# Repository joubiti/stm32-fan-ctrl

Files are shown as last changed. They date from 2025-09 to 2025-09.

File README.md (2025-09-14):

# 12V Fan Controller with STM32 and PID control
## Overview

This project implements a closed-loop fan controller on a custom 4-layer PCB (manufactured at JLCPCB) with an STM32G0 micrcontroller.
The fan speed is controlled using a PWM signal and regulated to a target RPM using a PID controller.
The tachometer output of the fan is measured with a timer input capture unit, filtered, and fed into the control loop.
Fairly satisfactory control performances have been achieved with Kp=0.01, Ki=0.015, and Kd = 0.001 at 10Hz.



## Hardware features

4 layer board designed with KiCAD, and manufactured at JLCPCB for roughly 100 euros total (including shipping) for 2PCBA and 3PCBs, very minimal and cheap BOM. Production files are in Hardware/Production.

* **Buck Converter** takes 12V input from DC input jack and generates 5V rail (for PWM)
* **Linear Regulator** generates 3.3V rail from 5V (for MCU signals)
* **N-channel MOSFET** for low-side switching to generate appropriate PWM signals for 4-wire fan, inverting logic in firmware
* **Tachometer** open collector input for fan RPM measurement (hardware timer)

Schematics are given below:



PCB layout:



3D view:



Manufactured & assembled boards:





## System Architecture

* **Tachometer**: Measures period between tach pulses, converts to RPM (tachometer.h, tachometer.c)
* **First order IIR low pass filter**: Smooths RPM measurement (low_pass_filter.h, low_pass_filter.c)
* **PID controller**: Computes duty cycle command from target vs. measured RPM (pid_controller.h, pid_controller.c)
* **Fan speed controller**: Applies PWM duty cycle to MOSFET (fan_speed_controller.h, fan_speed_controller.c)
* **Application loop**: Handles control functions at 10 Hz, heartbeat at 1Hz, logging at 0.5Hz

```
  while (1)
  {
    /**************************** CONTROL LOOP (10 Hz) ****************** */
    tachometer_update_rpm(&fan_tachometer, HAL_GetTick());
    low_pass_filter_update(&rpm_filter, fan_tachometer.current_rpm, HAL_GetTick());
    uint8_t command = pid_controller_step(&pid, (uint32_t)rpm_filter.last_sample, RPM_SETPOINT, HAL_GetTick());
    if(command != PID_NO_UPDATE)
    {
      fan_set_rpm_percent(&fan_controller, command);
    }
    /******************************************************************** */

    /************************** HEARTBEAT LED & PERIODIC UART MESSAGES ****** */
    heartbeat_toggle(&heartbeat_led, HAL_GetTick());
    logging_send_periodic_msg(HAL_GetTick(), "Fan RPM: %d \n", fan_tachometer.current_rpm);
    /************************************************************************ */
  }
```

## System performances

After tuning PID controller and testing various setpoints, we have reached the following system response.

For 5000 RPM:

For 8000 RPM:

It's possible to achieve better performances, but for the sake of this project and for my use-case, this is satisfying enough.
The plots were generated with MCUViewer, which enables live capture of global variables with static addresses through SWD/JTAG.



## Building

To build the code, it is enough to run "make" in the "Software" directory. Assuming arm-none-eabi-gcc is correctly installed and configured for $PATH.
KiCAD Files are provided in Hardware/, and JLCPCB production files in Hardware/Production.

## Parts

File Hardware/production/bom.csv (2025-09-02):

Designator | Footprint | Quantity | Value | LCSC Part #
C1, C2, C3, C7 | 0402 | 4 | 100n
C10, C11, C12, C13, C8 | 1206 | 5 | 10u
C4 | 0402 | 1 | 4.7u
C5, C6 | 0402 | 2 | 10p
C9 | 1206 | 1 | 10n
CN1 | CONN-TH_4P-P3.50_DIBO_DB127S-3.5-4P-GN | 1 | DB127S-3.5-4P-GN | C2997511
D1 | 0805 | 1 | LED
D2 | 0402 | 1 | LED
D3 | SOD-123_L2.7-W1.6-LS3.7-RD-1 | 1 | B5819W_C8598 | C8598
F1 | 1206 | 1 | 500mA
FB1 | 1206 | 1 | 600 @ 600 MHz
L1 | 1206 | 1 | 4.7u
Q1 | SOT-23_L2.9-W1.3-P1.90-LS2.4-BR | 1 | AO3401A | C15127
Q2 | Q_SOT-23 | 1 | AO3400A | C20917
R1 | R_0603 | 1 | 49k9
R10, R13, R9 | R_0603 | 3 | 10k
R11, R3 | R_0402 | 2 | 10k
R12 | R_0402 | 1 | 100
R2, R8 | R_0402 | 2 | 1k
R4 | R_0603 | 1 | 100k
R7 | R_0603 | 1 | 9k1
TP1, TP2, TP3, TP5, TP6 | TestPoint_Pad_D3.0mm | 5 | TestPoint
TP10, TP11, TP9 | TestPoint_THTPad_D1.0mm_Drill0.5mm | 3 | TestPoint
TP4, TP7, TP8 | TestPoint_Pad_D2.0mm | 3 | TestPoint
U1 | LQFP-64_L10.0-W10.0-P0.50-LS12.0-BL | 1 | STM32G070RBT6 | C529340
U2, U3 | HDR-TH_3P-P2.54-V-M-1 | 2 | 826629-3 | C306127
U4 | SOT-23-6_L2.9-W1.6-P0.95-LS2.8-BR | 1 | MP2359DT-LF-Z | C6595509
U5 | DC-IN-TH_XDJK-0051-025 | 1 | XDJK-0051-025 | C7498153
U6 | SOT-223-3_TabPin2 | 1 | AMS1117-3.3
Y1 | Crystal_SMD_3225-4Pin_3.2x2.5mm | 1 | Crystal_GND24

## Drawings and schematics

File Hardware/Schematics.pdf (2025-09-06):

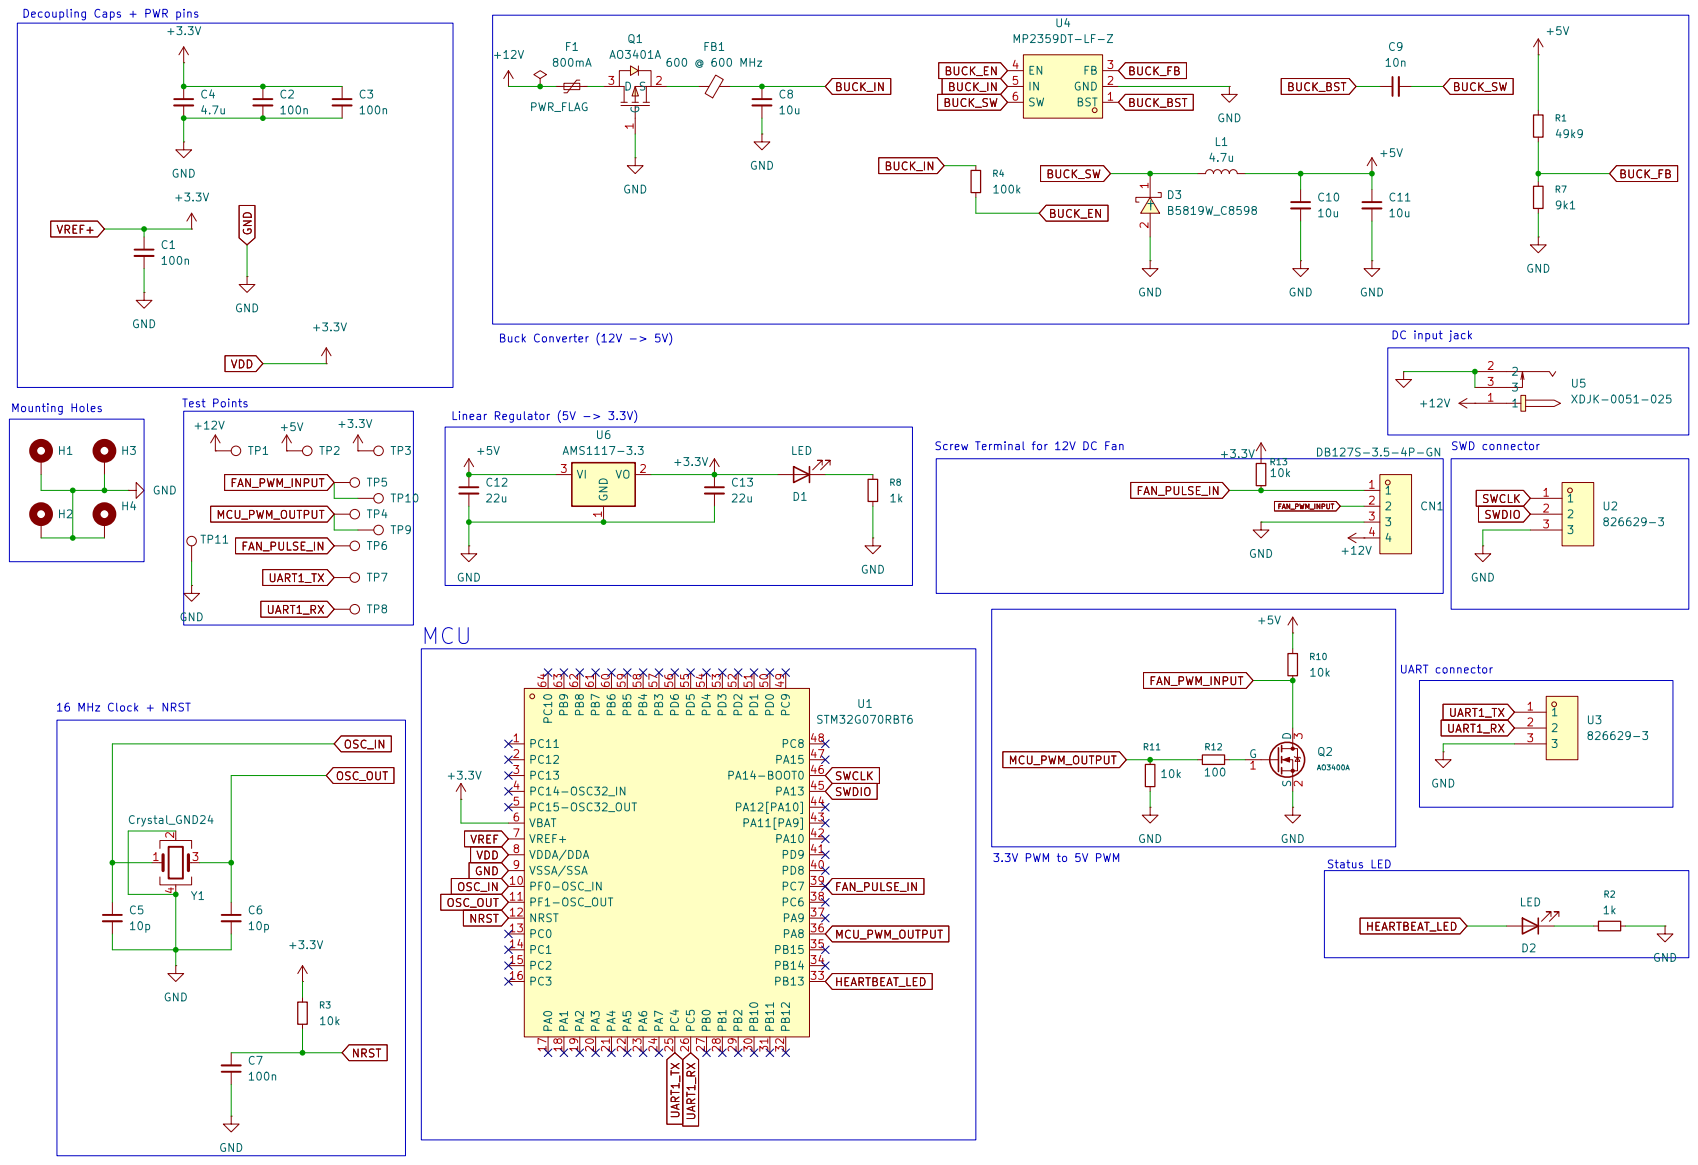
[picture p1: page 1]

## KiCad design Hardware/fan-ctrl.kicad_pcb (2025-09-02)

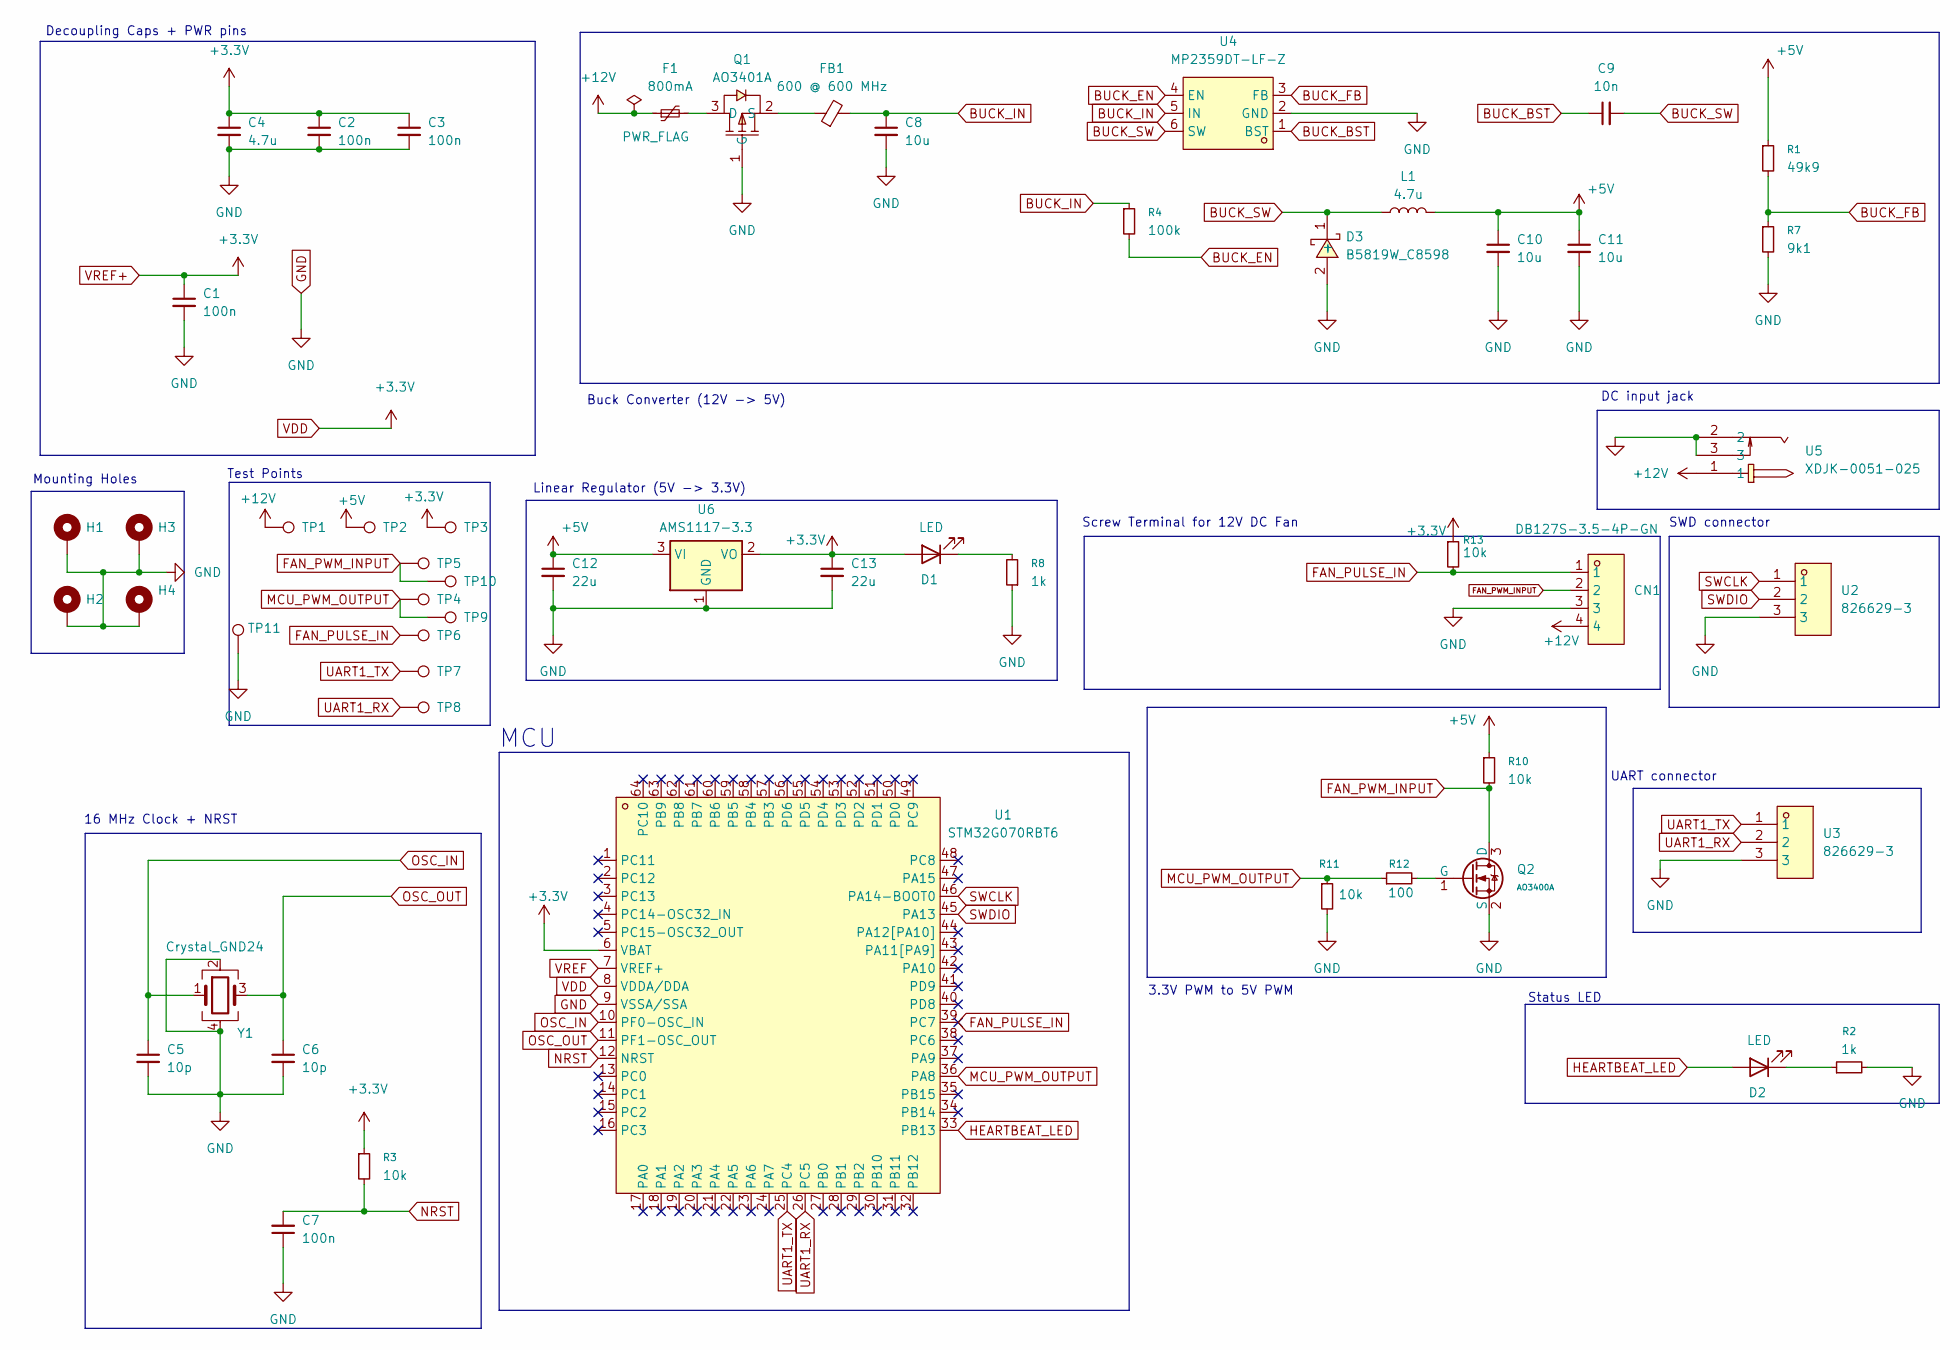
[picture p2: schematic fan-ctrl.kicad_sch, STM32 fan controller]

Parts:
C1, C2, C3, C7: 100n; C_0402_1005Metric
C4: 4.7u; C_0402_1005Metric
C5, C6: 10p; C_0402_1005Metric
C8, C10, C11: 10u; C_1206_3216Metric
C9: 10n; C_1206_3216Metric
C12, C13: 22u; C_1206_3216Metric
CN1: DB127S-3.5-4P-GN; CONN-TH_4P-P3.50_DIBO_DB127S-3.5-4P-GN; LCSC Part C2997511
D1: LED; LED_0805_2012Metric
D2: LED; LED_0402_1005Metric
D3: B5819W_C8598; SOD-123_L2.7-W1.6-LS3.7-RD-1; LCSC Part C8598
F1: 800mA; Fuse_1206_3216Metric
FB1: 600 @ 600 MHz; L_1206_3216Metric
H1, H2, H3, H4: MountingHole_Pad; MountingHole_2.2mm_M2_Pad_Via
L1: 4.7u; L_1206_3216Metric
Q1: AO3401A; SOT-23_L2.9-W1.3-P1.90-LS2.4-BR; LCSC Part C15127
Q2: AO3400A; Q_SOT-23; Part AO3400A; LCSC C20917
R1: 49k9; R_0603
R2, R8: 1k; R_0402
R3, R11: 10k; R_0402
R4: 100k; R_0603
R7: 9k1; R_0603
R10, R13: 10k; R_0603
R12: 100; R_0402
TP1, TP2, TP3, TP5, TP6: TestPoint; TestPoint_Pad_D3.0mm
TP4, TP7, TP8: TestPoint; TestPoint_Pad_D2.0mm
TP9, TP10, TP11: TestPoint; TestPoint_THTPad_D1.0mm_Drill0.5mm
U1: STM32G070RBT6; LQFP-64_L10.0-W10.0-P0.50-LS12.0-BL; LCSC Part C529340
U2, U3: 826629-3; HDR-TH_3P-P2.54-V-M-1; LCSC Part C306127
U4: MP2359DT-LF-Z; SOT-23-6_L2.9-W1.6-P0.95-LS2.8-BR; LCSC Part C6595509
U5: XDJK-0051-025; DC-IN-TH_XDJK-0051-025; LCSC Part C7498153
U6: AMS1117-3.3; SOT-223-3_TabPin2
Y1: Crystal_GND24; Crystal_SMD_3225-4Pin_3.2x2.5mm

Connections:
+5V: C10.1, C11.1, C12.1, L1.2, R1.1, R10.1, TP2.1, U6.3 (VI)
+12V: CN1.4, F1.1, TP1.1, U5.1
BUCK_BST: C9.1, U4.1 (BST)
BUCK_EN: R4.2, U4.4 (EN)
BUCK_FB: R1.2, R7.1, U4.3 (FB)
BUCK_IN: C8.1, FB1.2, R4.1, U4.5 (IN)
BUCK_SW: C9.2, D3.1 (-), L1.1, U4.6 (SW)
FAN_PULSE_IN: CN1.1, R13.2, TP6.1, U1.39 (PC7); also elsewhere on the board
FAN_PWM_INPUT: CN1.2, Q2.3 (D), R10.2, TP5.1, TP10.1
GND: C1.2, C2.2, C3.2, C4.2, C5.2, C6.2, C7.1, C8.2, C10.2, C11.2, C12.2, C13.2, CN1.3, D3.2 (+), H1.1, H2.1, H3.1, H4.1, Q1.1 (G), Q2.2 (S), R2.2, R7.2, R8.1, R11.2, TP11.1, U1.9 (VSSA/SSA), U2.3, U3.3, U4.2 (GND), U5.2, U5.3, U6.1 (GND), Y1.2, Y1.4
HEARTBEAT_LED: D2.2 (A), U1.33 (PB13)
MCU_PWM_OUTPUT: R11.1, R12.1, TP4.1, TP9.1, U1.36 (PA8)
NRST: C7.2, R3.2, U1.12 (NRST)
unnamed: D1.1 (K), R8.2
unnamed: D2.1 (K), R2.1
unnamed: F1.2, Q1.3 (D)
unnamed: FB1.1, Q1.2 (S)
unnamed: Q2.1 (G), R12.2
OSC_IN: C5.1, U1.10 (PF0-OSC_IN), Y1.1
OSC_OUT: C6.1, U1.11 (PF1-OSC_OUT), Y1.3
SWCLK: U1.46 (PA14-BOOT0), U2.1
SWDIO: U1.45 (PA13), U2.2
UART1_RX: TP8.1, U1.26 (PC5), U3.2
UART1_TX: TP7.1, U1.25 (PC4), U3.1
VDD: C1.1, C2.1, C3.1, C4.1, C13.1, D1.2 (A), R3.1, R13.1, TP3.1, U1.6 (VBAT), U1.8 (VDDA/DDA), U6.2 (VO); also elsewhere on the board
VREF: U1.7 (VREF+)

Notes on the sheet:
MCU
UART connector
Buck Converter (12V -> 5V)
Linear Regulator (5V -> 3.3V)
Status LED
Screw Terminal for 12V DC Fan
Test Points
16 MHz Clock + NRST
SWD connector
DC input jack
Decoupling Caps + PWR pins
3.3V PWM to 5V PWM
Mounting Holes

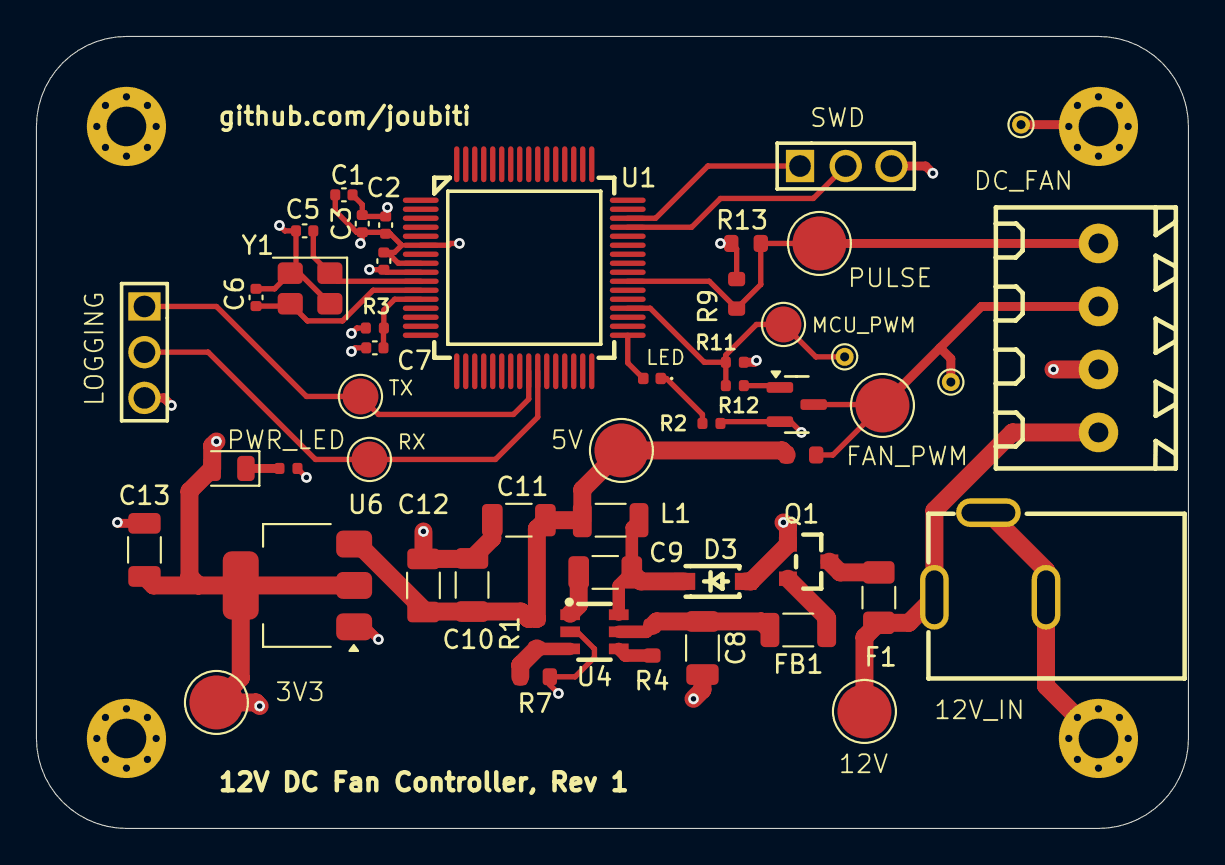
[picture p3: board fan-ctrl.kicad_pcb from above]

Board: 4 copper layers, 64.0 x 44.0 mm, 55 parts (0 on the bottom side), 25 nets.

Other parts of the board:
R9: 10k; R_0603

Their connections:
FAN_PULSE_IN: R9.2; also elsewhere on the board
VDD: R9.1; also elsewhere on the board

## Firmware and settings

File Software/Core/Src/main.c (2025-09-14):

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
/* Includes ------------------------------------------------------------------*/
#include "main.h"

/* USER CODE BEGIN PD */
#define RPM_SETPOINT 5000
#define CONTROL_LOOP_PERIOD_MS 100
/* USER CODE END PD */

TIM_HandleTypeDef htim1;
TIM_HandleTypeDef htim3;

UART_HandleTypeDef huart1;

void SystemClock_Config(void);
static void MX_GPIO_Init(void);
static void MX_TIM3_Init(void);
static void MX_USART1_UART_Init(void);
static void MX_TIM1_Init(void);
/* USER CODE BEGIN 0 */
static heartbeat_led_t heartbeat_led;
static tachometer_t fan_tachometer;
static fan_controller_t fan_controller;
static pid_controller_t pid;
static lp_filter_t rpm_filter;

static volatile uint8_t command = 0;



/* USER CODE END 0 */

/**
  * @brief  The application entry point.
  * @retval int
  */
int main(void)
{

  /* MCU Configuration--------------------------------------------------------*/

  /* Reset of all peripherals, Initializes the Flash interface and the Systick. */
  HAL_Init();

  /* Configure the system clock */
  SystemClock_Config();

  /* Initialize all configured peripherals */
  MX_GPIO_Init();
  MX_TIM3_Init();
  MX_USART1_UART_Init();
  MX_TIM1_Init();
  /* USER CODE BEGIN 2 */
  




  /********** Fan Speed controller (PWM) ************/

  fan_speed_controller_init(&fan_controller, &htim1);
  fan_set_rpm_percent(&fan_controller, 0);
  
  /************************************************ */
  /* Initialize logging subsystem, mapped to UART1 */

  logging_subsystem_init(&huart1);
  logging_set_message_frequency(2000);

  /***********************************************/
  /********* Initialize heartbeat LED (1 Hz)******/

  heartbeat_initialize(&heartbeat_led, 1000);
  heartbeat_on(&heartbeat_led);

  /**********************************************/
  /*********** Fan DC speed sensor **************/

  tachometer_init(&fan_tachometer, &htim3, CONTROL_LOOP_PERIOD_MS);

  /******************************************** */
  /****** First order LP filter for Tachometer **/

  low_pass_filter_init(&rpm_filter, 0.3, CONTROL_LOOP_PERIOD_MS);
  
  /******************************************************* */
  /*****************   PID controller ******************** */

  pid_controller_init(&pid, 0.01, 0.015, 0.001, CONTROL_LOOP_PERIOD_MS);

  /*********************************************************/









  /* USER CODE END 2 */

  /* Infinite loop */
  /* USER CODE BEGIN WHILE */
  while (1)
  {
    /* USER CODE END WHILE */

    /* USER CODE BEGIN 3 */



    /**************************** CONTROL LOOP (10 Hz) ****************** */
    tachometer_update_rpm(&fan_tachometer, HAL_GetTick());
    low_pass_filter_update(&rpm_filter, fan_tachometer.current_rpm, HAL_GetTick());
    uint8_t command = pid_controller_step(&pid, (uint32_t)rpm_filter.last_sample, RPM_SETPOINT, HAL_GetTick());
    if(command != PID_NO_UPDATE)
    {
      fan_set_rpm_percent(&fan_controller, command);
    }
    /******************************************************************** */




    /************************** HEARTBEAT LED & PERIODIC UART MESSAGES ****** */
    heartbeat_toggle(&heartbeat_led, HAL_GetTick());
    logging_send_periodic_msg(HAL_GetTick(), "Fan RPM: %d \n", fan_tachometer.current_rpm);
    /************************************************************************ */




  }
  /* USER CODE END 3 */
}

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


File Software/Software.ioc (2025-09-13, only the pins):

Mcu.UserName=STM32G070RBTx
PA13.Signal=SYS_SWDIO
PA14-BOOT0.Signal=SYS_SWCLK
PA8.Signal=S_TIM1_CH1
PB13.Signal=GPIO_Output
PC4.Signal=USART1_TX
PC5.Signal=USART1_RX
PC7.Signal=S_TIM3_CH2

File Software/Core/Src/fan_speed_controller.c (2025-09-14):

/**
 * @file fan_speed_controller.c
 * @author your name (you@domain.com)
 * @brief 
 * @version 0.1
 * @date 2025-09-13
 * 
 * @copyright Copyright (c) 2025
 * 
 */

#include "fan_speed_controller.h"

#include "stdlib.h"

#define FAN_PWM_CHANNEL TIM_CHANNEL_1

/**
 * @brief Macro helper to get ARR register value from PWM duty cycle
 * 
 */
#define get_pwm_compare_value(x) (uint16_t)((x * 24999)/100)


void fan_speed_controller_init(fan_controller_t* fan, TIM_HandleTypeDef* htim)
{
    fan->htim = htim;
    fan->rpm_measured = 0;
    fan->rpm_requested = 0;

    // start PWM timer
    HAL_TIM_Base_Start(fan->htim);
    HAL_TIM_PWM_Start(fan->htim, TIM_CHANNEL_1);
}


void fan_set_rpm_percent(fan_controller_t* fan, uint8_t percent)
{
    if(percent > 100)
        percent = 100;
    uint8_t scaled_percent = 100 - percent;
    __HAL_TIM_SET_COMPARE(fan->htim, FAN_PWM_CHANNEL, get_pwm_compare_value(scaled_percent));
}

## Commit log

2025-08-30 Initial layout (MCU, crystal circuitry, buck converter)
    [fan-ctrl.kicad_pcb, fan-ctrl.kicad_sch]
2025-08-31 Update buck converter circuit (5V output), add switching linear regulator for 3.3V output, add N-channel MOSFET for 5V PWM control
    [fan-ctrl.kicad_sch]
2025-08-31 Add mounting holes, test points, initial footprint assignment, next up:review design and buck converter output, review available footprints in JLCPCB
    [fan-ctrl.kicad_pcb, fan-ctrl.kicad_sch]
2025-08-31 Component placement, board edge cuts, adjust some footprints, testpoints, silkscreen for connectors and testpoints, next: review footprints JLCPCB before routing
    [fan-ctrl.kicad_pcb, fan-ctrl.kicad_sch]
2025-08-31 Adjust board dimensions and edge cuts
    [fan-ctrl.kicad_pcb]
2025-09-01 Update buck converter circuit, standard R values for close 5V output, double-checked footprints available in JLCPCB
    [fan-ctrl.kicad_pcb, fan-ctrl.kicad_sch]
2025-09-02 Update schematics (polyfuse value, capacitor values in linear regulatorcircuit, use different HW timer enabled pin for the fan pulse input
    [bom.csv, designators.csv, fan-ctrl.kicad_pcb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]
2025-09-06 Add board schematics to readme
2025-09-06 Update KiCAD project, add schematics .pdf
2025-09-06 Add 3D of board
2025-09-08 Received PCBs from JLC, board bring-up: heartbeat LED OK, next up: UARTinterface
2025-09-08 Push logging module, UART working on board, next up: 50% square wave on PWM
2025-09-09 Board bring-up: defining timer for input capture and frequency measurement. 0% duty cycle means fan running at very low speeds, 100% is max speed
2025-09-12 First prototype of tachometer module, seems to be roughly OK (timer sampling at 1 MHz), to do: handle overflows and moving average filter
2025-09-13 Add fan speed controller module, for 0-100% speed modulation based on PWM
2025-09-14 Implement and tune PID controller, implement first order IIR low pass filter for tachometer reading, minor adjustments in main loop

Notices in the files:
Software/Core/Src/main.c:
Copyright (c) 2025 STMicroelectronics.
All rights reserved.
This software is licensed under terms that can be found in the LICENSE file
